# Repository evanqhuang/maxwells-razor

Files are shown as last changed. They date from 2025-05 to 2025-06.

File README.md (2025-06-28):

<p align="center">
 
</p>
<h2 align="center">
A simpler, modular, 90% 3D printed, 3D printer toolchanger
 
Maxwell Coupling + Occam's Razor



</h2>
<p align="center">

</video>
</p>

## Table of Contents
- [About](#about)
- [Why toolchangers?](#why-toolchangers)
- [Contributions](#contributions)
- [Disclaimer](#disclaimer)
- [License](#license)

## About

Typical 3D printed gadgets are laden with hyper specific parts that increases the BOM cost significantly. I tried to find a completely mechanical toolchanger and only found over-engineered designs with large BOM's and complex assembly. I designed Maxwell's Razor to use as few non-printed parts as possible, the coupling is entirely 3D printed with the most special part being a few neodymium magnets to securely attach the printheads to the gantry. In addition, the docking mechanism is completely mechanical and 3D printed as well. Estimated cost per toolhead (including hotend and stepper) is well under 20USD. Most of the cost comes from the extra stepper and E3D V6 hotend, the design only uses 1 USD worth of magnets for each toolhead. 

I took inspiration from the [Maxwell kinematic coupling](https://en.wikipedia.org/wiki/Kinematic_coupling) and applied [Occam's Razor](https://en.wikipedia.org/wiki/Occam%27s_razor) to the design process, the simplest solution is usually the best one. Originally, I had a press fit ball bearing on one side, with metal dowels on the other ([/metal]([./metal])). This worked great but I was dissapointed with the need to have 2 additional non printed parts, which can be hard to obtain. I was able to simplify this into a completely 3D printed coupling with [/v1](./v1).

Printing instructions are located in the respective folders for each version of the toolchanger, e.x. [/v1/README.md](./v1/README.md) or  [/metal/README.md](./metal/README.md). The current versions are only compatible with the Hypercube EVO (and maybe the original Hypercube, untested). All parts were prototyped with a refurbished Elegoo Neptune 4 I bought for 90USD and 12USD/kg PETG, so don't worry if you only have a cheap 3D printer. 

A major modification you will need is **sensorless homing**, this removes the need to redesign the X and Y endstops on the Hypercube and also makes it much easier to adapt the design to other printers. 

STEP files are also provided so that you can easily modify the parts for your use case. 

Special thanks to Scott3D for the [original Hypercube EVO design](https://www.thingiverse.com/thing:2254103).

### Why toolchangers?
Most widely available 3D printers only have a single extrusion head. The only commercially available toolchanging system is the [Prusa XL](https://www.prusa3d.com/en/product/original-prusa-xl-semi-assembled-2-toolhead-3d-printer/), which costs 2500USD as of writing, for just 2 printheads. 

Those with Bambu/Prusa printers might wonder about the [BambuLabs AMS](https://us.store.bambulab.com/collections/all-ams) and the [Prusa MMU](https://www.prusa3d.com/category/original-prusa-mmu3/). However, the major distinction is that these options are only **multi-color**. Because the printhead is shared between all filaments you can only print in a single material at once. This greatly limits the usefulness of the AMS in more technical applications. 

With multiple printheads, you can move beyond simple filament swapping and create complex parts. For example, you can print a hard PETG lid with an integrated, flexible TPU gasket, or a phone case that combines a rigid shell with shock-absorbing TPU. Another key benefit is being able to print support in a different material than the object. Since the materials don't bond, the supports pop right off and leave a flawless surface with no effort. 

Lastly, the modular nature of a toolchanger allows you to even create toolheads that aren't for extruding. Imagine printing a blank luggage tag, and then switching to a laser toolhead to engrave your contact information directly onto it in one go. 

## Contributions

If you've adapted the design for your use case, please don't hesitate to open a PR!

## Disclaimer
I am not a mechanical engineer or anything like that, just a hobbyist that's been involved in 3D printers since the RepRap days. Therefore, these modifications should be done at your own risk, etc. I am not liable for any damages that may occur as a result of the modifications in this repo.

## License

This project is distributed under the [CERN-OHL-W-2.0 license](https://github.com/evanqhuang/maxwells-razor/tree/main#CERN-OHL-W-2.0-1-ov-file). This means that modifications need to be distributed as open source. E.g. if you made a design for a Voron printer, you would have to openly distribute the modified parts only.

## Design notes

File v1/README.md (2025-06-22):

## BOM

### With an inductive Z probe sensor

#### For the X carriage coupling adapter
- **Follow [Print settings](#print-settings) below**
- `adapter.stl` and `probe_holder.stl`
- 6x - 12mm x 3mm neodymium magnets (recommended to be N42 or N52, weaker ones won't hold the printhead securely enough)
- 1x inductive sensor - fits up to an 18mm diameter sensor
- 1x 6mm M3 bolt - to secure the inductive sensor
- The adapter is the only piece that has a recommended high resolution layer height and ironing. You could have issues with mating if the adapter surface is not flat or if the half sphere is not as close to round as possible.

#### For each printhead
- **Follow [Print settings](#print-settings) below**
- `dock_left_hand.stl`
- `extruder_mount.stl`
- `retainer.stl`
- `shroud.stl`
- `hotend_cable_holder.stl`
- E3D V6 
- 5015 fan
- 2x - M3 heat set insert
- 3x - 12mm x 3mm neodymium magnets
- **The lengths below are what I used but you can easily use slightly different lengths based on what you have available**
- 20mm M3 bolt - for attaching part cooling fan
- 2x - 14mm M3 bolt - for attaching retainer to extruder mount
- 4x - 5mm M3 bolt - for attaching part cooling fan shroud and hotend cable holder

### Bring your own Z end stop solution
Same parts as above but instead of `adaptor.stl` and `probe_holder.stl` print `adapter_no_probe_holder.stl` 

## Print settings
- **Files are already in the correct orientation. PETG recommended, but I think PLA would be fine as well, just not as durable longterm.**

| File | Layer height | Walls (0.4mm nozzle) | Infill | Support | Support type | Ironing |
|--|--|--|--|--|--|--|
| `adapter.stl` | 0.1mm | 4 | 30% | :white_check_mark: | Normal | :white_check_mark: |  |
| `probe_holder.stl` | 0.2mm | 3 | 30% | :x: | :x: | :x: |
| `adapter_no_probe_holder.stl` | 0.1mm | 4 | 30% | :white_check_mark: | Normal | :white_check_mark: |
| `dock_left_hand.stl` | 0.2mm | 2 | 30% | :white_check_mark: | Tree | :x: |
| `dock_right_hand.stl` | 0.2mm | 2 | 30% | :white_check_mark: | Tree | :x: |
| `extruder_mount.stl` | 0.2mm | 4 | 30% | :x: | Normal | :x: |
| `retainer.stl` | 0.2mm | 4 | 30% | :x: | Normal | :x: |

These files don't have any specific print setting requirements:
- `hotend_cable_holder.stl` 
- `shroud.stl`
## Assembly 

**Assembling the adapter:**
- Attach `adapter.stl` and `probe_holder.stl` together with a bit of super glue
- Insert 2x magnets into each of the holes on the adapter - you might need super glue to secure them but it should be press fit
- Insert inductive sensor into `probe_holder.stl` and secure with the 17mm M3 bolt

**Assembling the extruder mount:**
 - Insert 1x magnet into each of the holes on the adapter - you might need super glue to secure them but it should be press fit
 - Take care to match the polarity, but if you get it wrong -  there are holes on the other side you can use to push out the magnet
 - Melt heat set inserts into "bridge" of the extruder mount, secure hotend with `retainer.stl` and 17mm M3 bolts
 - Self tap 23mm M3 bolt to attach 5015 fan
 - Self tap 8mm M3 bolt to attach `shroud.stl` and `hotend_cable_holder.stl`

## Klipper Setup

- All necessary `.cfg` files are in [klipper_config](v1/klipper_config), place these in `printer_data/config/` on your raspberry pi
- Copy `printer_variables.cfg` as well to the home directory on your raspberry pi, this contains the variables for positioning the toolhead docks
- To set the position of the leftmost dock (which is T1 in the config):
- Partially secure the dock to the frame, then
  ```
  ALIGN_DOCK
  ```
  This will position the carriage right where the `PICK_extruder` macro expects the toolhead to be. Then, slide the dock into the correct position, the magnets will lock it into place. Tighten the screws and repeat for the next dock with:
  ```
  ALIGN_DOCK1
  ```

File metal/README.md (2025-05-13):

## NOTE: PROTOTYPE UNTESTED 
This is mostly to keep track of a POC using more non-printed parts, this is not fully completed.

## BOM
- **Follow [Print settings](#print-settings) below**
- `extruder_mount.stl`
- `x_carriage.stl`
- 6x - 10mm x 2mm neodymium magnets (recommended to be N42 or N52, weaker ones won't hold the printhead securely enough)
- 3x - 4mm ball bearing
- 6x - 12mm x 3mm metal dowel

## Print settings

| File | Layer height | Walls (0.4mm nozzle) | Infill | Support | Support type | Ironing |
|--|--|--|--|--|--|--|
| `x_carriage.stl` | 0.1mm | 4 | 30% | :white_check_mark: | Normal | :white_check_mark: |  |
| `extruder_mount.stl` | 0.2mm | 4 | 30% | :white_check_mark: | Normal | :x: |

## Assembly 

Should be pretty self explanatory, you may need to heat up the bearings a little to be able to press fit them into the holes

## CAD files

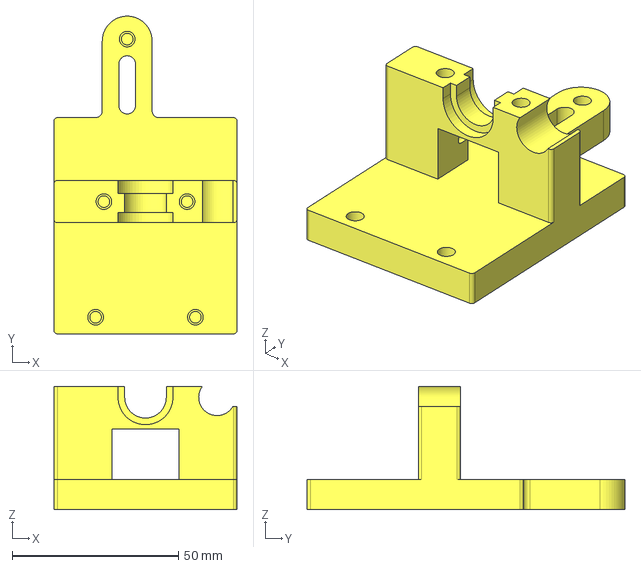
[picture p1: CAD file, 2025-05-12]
metal/STEP/extruder_mount.step
55.0 x 95.5 x 37.0 mm

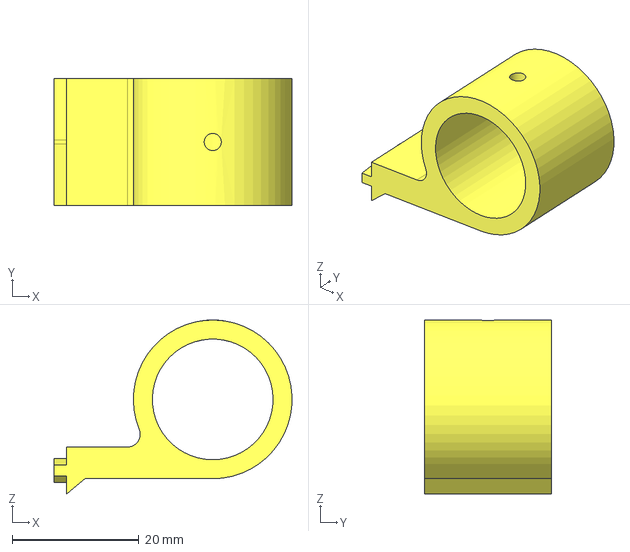
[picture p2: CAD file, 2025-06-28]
v1/STEP/probe_holder.step
37.5 x 20.0 x 27.4 mm

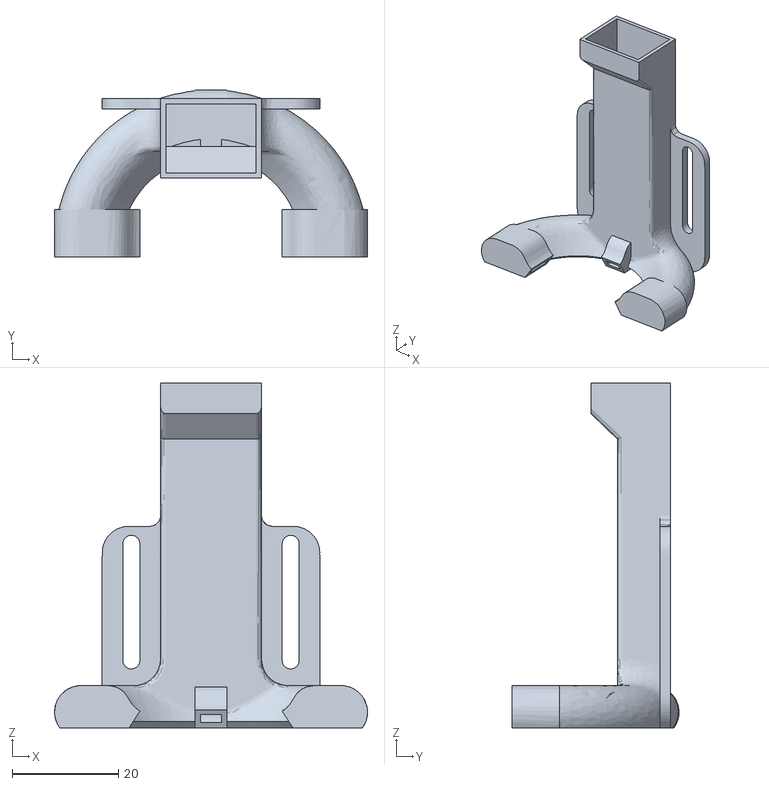
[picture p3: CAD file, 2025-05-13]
v1/STL/shroud.stl
59.0 x 31.5 x 65.0

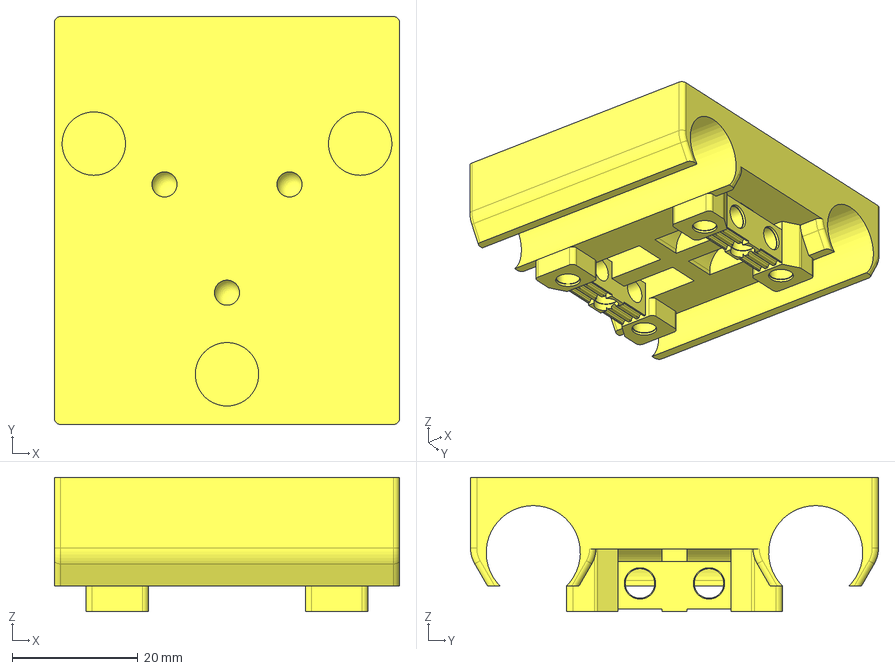
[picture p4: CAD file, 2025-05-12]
metal/STEP/x_carriage.step
55.0 x 65.0 x 21.4 mm

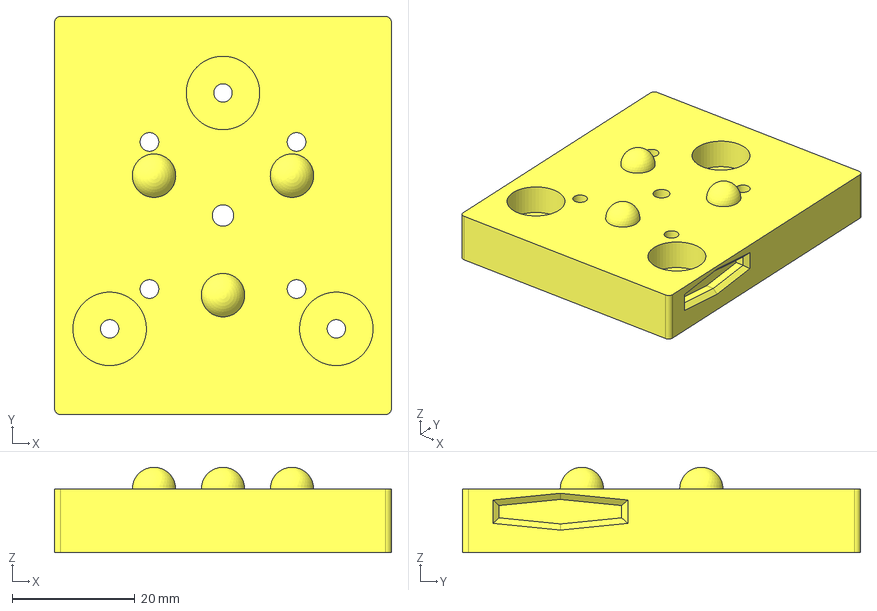
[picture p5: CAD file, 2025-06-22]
v1/STEP/adapter.step
55.0 x 65.0 x 14.0 mm

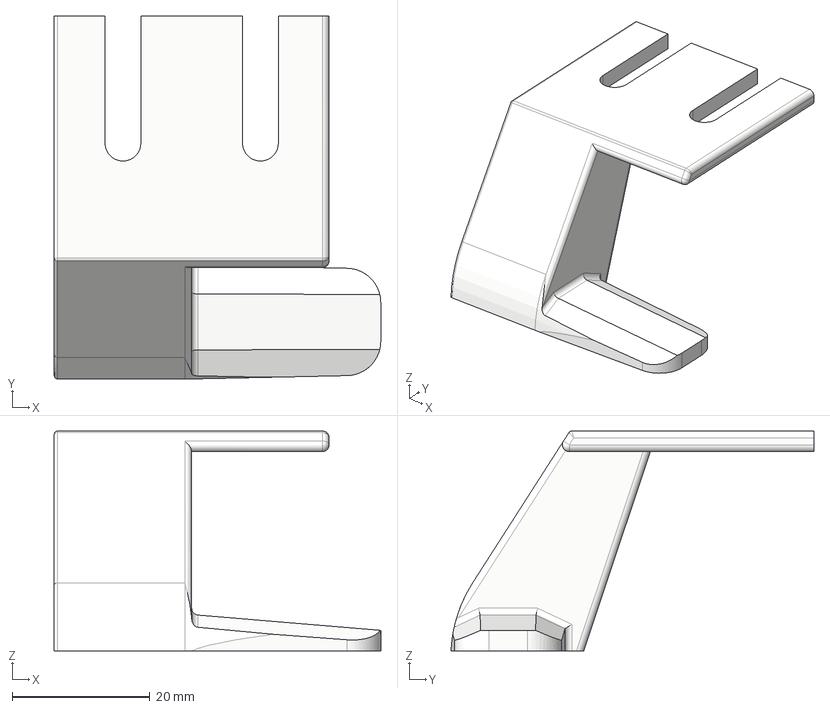
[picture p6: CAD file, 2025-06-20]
v1/STEP/dock_left_hand.step
47.5 x 52.8 x 32.0 mm
dock

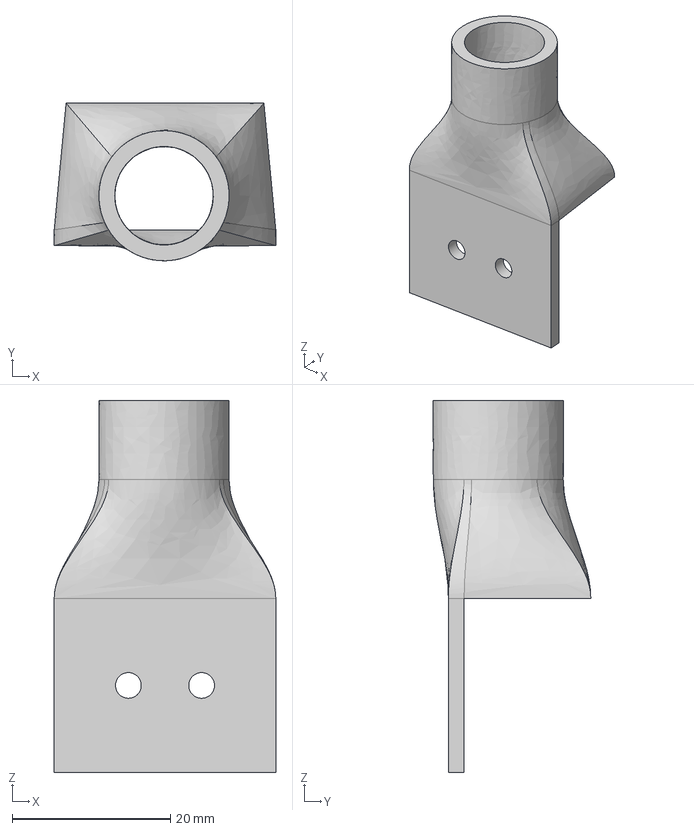
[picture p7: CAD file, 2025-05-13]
v1/STEP/hotend_cable_holder.step
28.0 x 19.9 x 47.0 mm

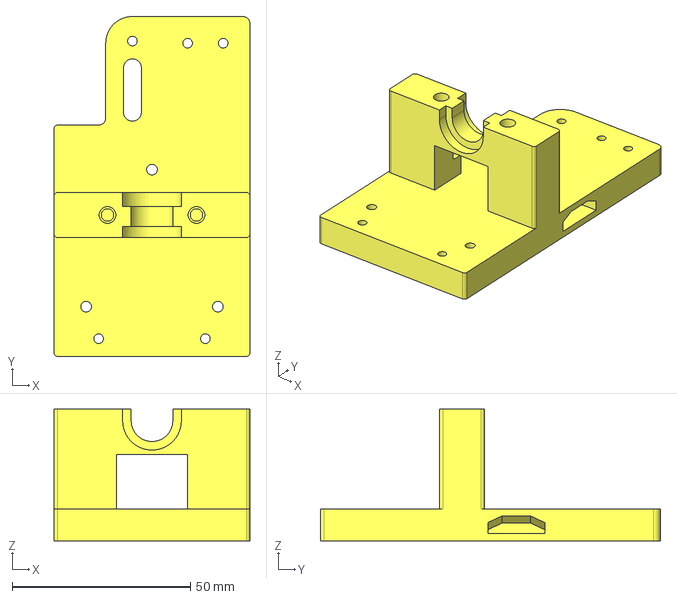
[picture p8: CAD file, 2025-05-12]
v1/STEP/extruder_mount.step
55.0 x 95.5 x 37.0 mm

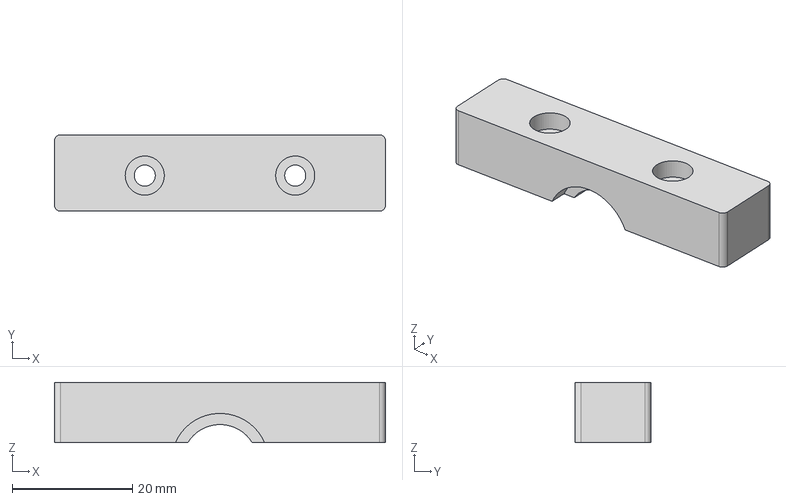
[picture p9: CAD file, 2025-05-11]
v1/STEP/retainer.step
55.0 x 12.7 x 10.0 mm

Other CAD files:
v1/STEP/dock_right_hand.step
v1/STEP/adapter_no_probe_holder.step
metal/STL/extruder_mount.stl
metal/STL/x_carriage.stl
v1/STL/adapter.stl
v1/STL/adapter_no_probe_holder.stl
v1/STL/dock_left_hand.stl
v1/STL/dock_right_hand.stl
v1/STL/extruder_mount.stl
v1/STL/hotend_cable_holder.stl
v1/STL/probe_holder.stl
v1/STL/retainer.stl

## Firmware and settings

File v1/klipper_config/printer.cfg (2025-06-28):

[include fluidd.cfg]
[include macros.cfg]
[include homing.cfg]
[include T0.cfg]
[include T1.cfg]

[force_move]
enable_force_move: True

[input_shaper]

[save_variables]
filename: ~/printer_variables.cfg


[gcode_macro FAKE_POSITION]
gcode:
  SET_KINEMATIC_POSITION X=10 Y=10 Z=10

[stepper_x]
step_pin: PF0 
dir_pin: PF1
enable_pin: !PD7 
microsteps: 16  
rotation_distance: 40.3
endstop_pin: tmc2209_stepper_x:virtual_endstop
position_endstop: 0
position_max: 210
position_min: -0.5
homing_speed: 20
homing_retract_dist: 0

[tmc2209 stepper_x]
uart_pin: PK1
tx_pin: PG1
diag_pin: ^PE5      # Set to MCU pin connected to TMC DIAG pin
driver_SGTHRS: 40  # 255 is most sensitive value, 0 is least sensitive
run_current: 0.8
stealthchop_threshold: 999999

[stepper_y]
step_pin: PF6
dir_pin: PF7
enable_pin: !PF2
microsteps: 16
rotation_distance: 40
endstop_pin: tmc2209_stepper_y:virtual_endstop
position_endstop: 0
position_max: 240
position_min: -0.5
homing_speed: 20
homing_retract_dist: 0

[tmc2209 stepper_y]
uart_pin: PK2
tx_pin: PF5
diag_pin: ^PJ1      # Set to MCU pin connected to TMC DIAG pin
driver_SGTHRS: 40  # 255 is most sensitive value, 0 is least sensitive
run_current: 0.8
stealthchop_threshold: 999999

[stepper_z]
step_pin: PL3
dir_pin: PL1
enable_pin: !PK0
microsteps: 16
rotation_distance: 8.07
endstop_pin: probe: z_virtual_endstop
position_min: -5
position_max: 200

[tmc2209 stepper_z]
uart_pin: PK3
tx_pin: PL7
diag_pin: ^PA5      # Set to MCU pin connected to TMC DIAG pin
driver_SGTHRS: 255  # 255 is most sensitive value, 0 is least sensitive
run_current: 0.8

[heater_bed]
heater_pin: PH5
sensor_type: EPCOS 100K B57560G104F
sensor_pin: PK6
min_temp: -20
max_temp: 130

[verify_heater heater_bed]
max_error: 120
check_gain_time: 120
hysteresis: 5
heating_gain: 2

[probe]
pin: !PD3
x_offset: 52
y_offset: 35

[virtual_sdcard]
path: /home/pi/printer_data/gcodes

[fan]
pin: PH6

[mcu]
serial: /dev/serial/by-id/usb-1a86_USB_Serial-if00-port0

[printer]
kinematics: corexy
max_velocity: 300
max_accel: 20000
max_z_velocity: 5
max_z_accel: 100

# Common EXP1 / EXP2 (display) pins
[board_pins]
aliases:
    # Common EXP1 header found on many "all-in-one" ramps clones
    EXP1_1=PC0, EXP1_3=PH0, EXP1_5=PA1, EXP1_7=PA5, EXP1_9=<GND>,
    EXP1_2=PC2, EXP1_4=PH1, EXP1_6=PA3, EXP1_8=PA7, EXP1_10=<5V>,
    # EXP2 header
    EXP2_1=PB3, EXP2_3=PC6, EXP2_5=PC4, EXP2_7=PL0, EXP2_9=<GND>,
    EXP2_2=PB1, EXP2_4=PB0, EXP2_6=PB2, EXP2_8=PG0, EXP2_10=<RST>
    # Pins EXP2_1, EXP2_6, EXP2_2 are also MISO, MOSI, SCK of bus "spi"
    # Note, some boards wire: EXP2_8=<RST>, EXP2_10=PG0

# See the sample-lcd.cfg file for definitions of common LCD displays.

#*# <---------------------- SAVE_CONFIG ---------------------->
#*# DO NOT EDIT THIS BLOCK OR BELOW. The contents are auto-generated.
#*#
#*# [probe]
#*# z_offset = 4.928
#*#
#*# [bed_mesh default]
#*# version = 1
#*# points =
#*# 	-0.148791, -0.232013, -0.269841, -0.264797, -0.365672, -0.322800
#*# 	-0.113484, -0.171488, -0.181575, -0.168966, -0.148791, -0.252188
#*# 	-0.058003, -0.105919, -0.108441, -0.126094, -0.110963, -0.068091
#*# 	-0.030263, -0.075656, -0.080700, -0.098353, -0.090788, -0.080700
#*# 	-0.065569, -0.126094, -0.161400, -0.148791, -0.168966, -0.126094
#*# 	-0.143747, -0.211838, -0.249666, -0.247144, -0.252188, -0.206794
#*# tension = 0.2
#*# min_x = 52.0
#*# algo = lagrange
#*# y_count = 6
#*# mesh_y_pps = 2
#*# min_y = 60.0
#*# x_count = 6
#*# max_y = 235.0
#*# mesh_x_pps = 2
#*# max_x = 195.0
#*#
#*# [extruder]
#*#
#*# [heater_bed]
#*# control = pid
#*# pid_kp = 48.049
#*# pid_ki = 1.504
#*# pid_kd = 383.793

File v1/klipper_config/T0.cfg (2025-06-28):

[gcode_macro _PARK_extruder]
gcode:
    {% set svv = printer.save_variables.variables %}
    {% set dock_x = svv.dock_x %}
    {% set arm_length = svv.arm_length %}
    {% set feedrate = svv.toolchange_feedrate %}

    # align with dock
    G1 X{dock_x + arm_length} Y{svv.safe_y} F{feedrate}
    # align with arm
    G1 Y0 F{feedrate}
    # park onto arm
    G1 X{dock_x} F{feedrate}

    SAVE_VARIABLE VARIABLE=currenttool VALUE='"none"'

    # remove carriage from toolhead
    G1 Y{svv.safe_y} F{feedrate}

    SET_GCODE_OFFSET Z_ADJUST=-0.05  move=1 speed=100

[gcode_macro ALIGN_DOCK]
gcode: 
    {% set svv = printer.save_variables.variables %}
    {% set dock_x = svv.dock_x %}
    {% set arm_length = svv.arm_length %}
    {% set feedrate = svv.toolchange_feedrate %}

    # move to safe area
    G1 X{dock_x + arm_length} Y{svv.safe_y} F{feedrate}
    # align with dock
    G1 X{dock_x} Y20 F{feedrate}
    # attach to toolhead
    G1 X{dock_x} Y0 F{feedrate}

[gcode_macro _PICK_extruder]
gcode:
    {% set svv = printer.save_variables.variables %}
    {% set dock_x = svv.dock_x %}
    {% set arm_length = svv.arm_length %}
    {% set feedrate = svv.toolchange_feedrate %}
    {% set z_adj = svv.t0_z_adjust %}

    PARK_CURRENT
    ACTIVATE_EXTRUDER EXTRUDER=extruder

    # move to safe area
    G1 X{dock_x + arm_length} Y{svv.safe_y} F{feedrate}
    # align with dock
    G1 X{dock_x} Y20 F{feedrate}
    # attach to toolhead
    G1 Y0 F{feedrate}
    # remove toolhead from dock
    G1 X{dock_x + arm_length} F{feedrate}

    SAVE_VARIABLE VARIABLE=currenttool VALUE='"extruder"'

    # move to safe area
    G1 Y{svv.safe_y} F{feedrate}

    SET_GCODE_OFFSET Z_ADJUST={z_adj} move=1 speed=100
    G1

[gcode_macro T0]
gcode:
    {% set svv = printer.save_variables.variables %}
    {% if (svv.currenttool != "extruder") %}
        SAVE_GCODE_STATE NAME=park0
        _LIFT_CARRIAGE
        _PICK_EXTRUDER
        _LOWER_CARRIAGE
        RESTORE_GCODE_STATE NAME=park0
    {% endif %}

[extruder]
step_pin: PA4
dir_pin: PA6
enable_pin: !PA2
microsteps: 16
full_steps_per_rotation: 200
gear_ratio: 50:17
rotation_distance: 23.056
nozzle_diameter: 0.400
filament_diameter: 1.750
heater_pin: PB4
sensor_type: EPCOS 100K B57560G104F
sensor_pin: PK5
control: pid
pid_Kp: 22.2
pid_Ki: 1.08
pid_Kd: 114
min_temp: -273
max_temp: 2500
max_extrude_only_distance: 300
pressure_advance: 0.25
max_extrude_only_velocity: 80
max_extrude_only_accel: 5000
max_extrude_cross_section: 50

[tmc2209 extruder]
uart_pin: PK4
tx_pin: PL5
run_current: 0.8

[verify_heater extruder]
max_error: 200
check_gain_time: 120
hysteresis: 20
heating_gain: 0.5

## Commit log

2025-05-11 upload v1
    [adapter.step, adapter.stl, adapter_no_probe_holder.step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]
2025-05-12 add prototype metal version
    [extruder_mount.step, extruder_mount.stl, x_carriage.step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]
2025-05-12 fix orientation and add readme
    [adapter.step, adapter.stl, dock_left_hand.stl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]
2025-05-12 changing to use 12x3mm magnets and adjusting location of z probe
    [adapter.step, adapter.stl, adapter_no_probe_holder.step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]
2025-05-12 making dock fit more securely
    [dock_left_hand.step, dock_left_hand.stl, dock_right_hand.step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]
2025-05-12 make extruder mount into 2 parts for easier/faster printing
    [extruder_mount.step, extruder_mount.stl, probe_holder.step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]
2025-05-12 fix orientation of dock
    [dock_left_hand.stl, dock_right_hand.stl]
2025-05-12 fix files
    [adapter.step, adapter.stl, extruder_mount.step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]
2025-05-13 add more files
    [hotend_cable_holder.step, hotend_cable_holder.stl, shroud.stl]
2025-05-13 increase depth of cutout
    [adapter.step, adapter.stl]
2025-05-13 add readme to metal and update folder structure
    [extruder_mount.step, extruder_mount.stl, x_carriage.step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]
2025-05-13 make dock fit more securely
    [dock_left_hand.step, dock_left_hand.stl, dock_right_hand.step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]
2025-06-20 add klipper config
    [T0.cfg, T1.cfg, fluidd.cfg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]
2025-06-20 adjust probe holder
    [probe_holder.step, probe_holder.stl]
2025-06-20 fix sym links
    [T0.cfg, T1.cfg, fluidd.cfg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]
2025-06-20 decrease probe holder protrusion
    [adapter.step, adapter.stl, probe_holder.step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]
2025-06-20 make dock more compact
    [dock_left_hand.step, dock_left_hand.stl, dock_right_hand.step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]
2025-06-22 fix a bunch of issues with toolchanging
    [T0.cfg, T1.cfg, homing.cfg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]
2025-06-22 fix bugs and adjust spacing
    [T0.cfg, T1.cfg, homing.cfg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]
2025-06-22 chamfer probe holder insert
    [adapter.step, adapter.stl]
2025-06-22 use variables to set dock pos and cleanup
    [T0.cfg, T1.cfg, homing.cfg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]
2025-06-22 remove toolchanger.cfg
    [toolchanger.cfg]
2025-06-23 add var for safe y
    [T0.cfg, T1.cfg, printer_variables.cfg]
2025-06-28 increase probe holder spacing
    [probe_holder.step, probe_holder.stl]
2025-06-28 use var for toolchange feedrate and make toolchange more robust
    [T0.cfg, T1.cfg, printer_variables.cfg]
2025-06-28 make homing more robust
    [homing.cfg, macros.cfg, printer.cfg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]
2025-06-28 add option for z adjust per tool
    [T0.cfg, T1.cfg, printer_variables.cfg]
